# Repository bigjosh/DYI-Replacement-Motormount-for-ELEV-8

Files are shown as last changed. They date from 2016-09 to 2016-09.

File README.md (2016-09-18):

# DYI-Replacement-Motormount-for-ELEV-8
Files for making your own replacement motor mounts for the [Parallax ELEV-8 drone](https://www.parallax.com/product/elev-8)

###Crash!

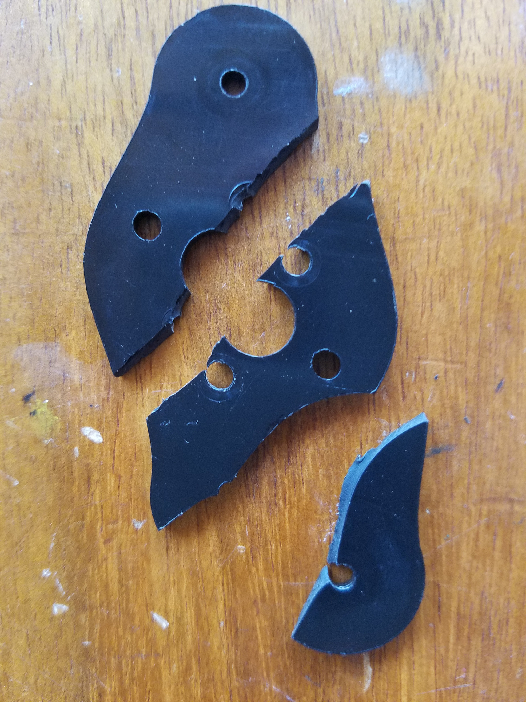
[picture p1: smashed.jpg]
smashed mount


I crashed my Parallax ELEV-8 drone (testing some stuff for Makerfaire NYC 2016!). 

The motormounts were smashed so I checked if I could...

###[Buy replacement motomounts directly from Parallax](https://www.parallax.com/product/721-80304)

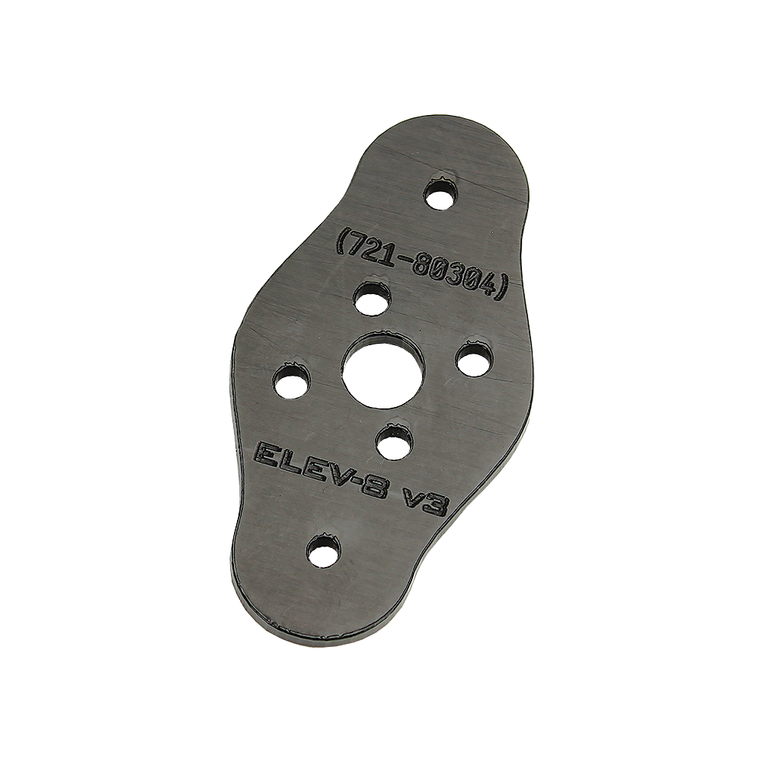
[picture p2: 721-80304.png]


Parallax sells the exact replacement part. They are made from 0.093 inches thick black acetal. They cost a reasonable for $3 each. 

Of course it is Friday night, so even if with an overnight shipping upgrade, I'd be grounded at least for the next 5 days. 

Maker Faire is 2 weeks away and there is (obviously) at least one crash-inducing problem to work out, so that wouldn't work. 

###Make replacement motor mounts!

I have a laser cutter, and converting bits into flat plastic shapes is exactly what laser cutters do best! Whoo hoo, I'll have my motormounts in no time!

###[Original SolidWorks file](721-80304.SLDPRT)

Parallax generously supplies files for all the parts in the ELEV-8!

But SolidWorks is [way too fancy](https://www.cati.com/blog/2015/04/how-much-does-solidworks-cost/) for me, so instead I import the part into...

###[OnShape](https://www.onshape.com/)

...which is a free and pretty nice web-based 3D cad program that happens to be able to import SolidWorks files. 

Here is what I ended up with...

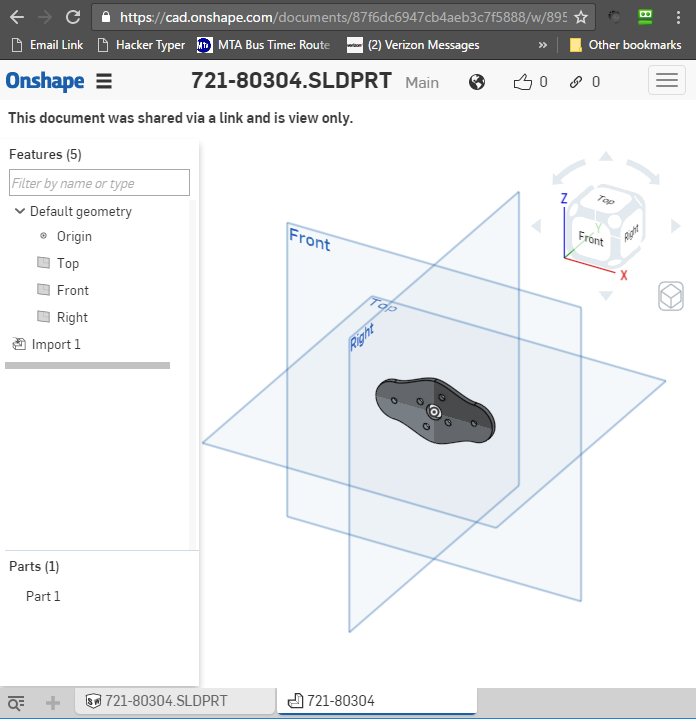
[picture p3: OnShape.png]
OnShape


https://cad.onshape.com/documents/87f6dc6947cb4aeb3c7f5888/w/89525256ab03b4d9a79cea25/e/45e0d6c32f898424b1c1b571

That looks familiar! I'll take 4 of those to go please!

I exported the face to a flat DXF R13 file...

[721-80304 - Face.dxf](721-80304 - Face.dxf)

Unfortunately my laser cutter does not speak DXF, but I can import the DXF into...

###[Inkscape](https://inkscape.org/en/)

...which is a free program that can import DXF and export the SVG files my laster cutter craves!

Sadly, Inkscape balked at the DXF (as often happens with DXF files) with a "POLYLINE encountered and ignored" error, so no joy on this path.

This must be my punishment for trying to use a cutting-edge web-based CAD tool. Serious people who want to get things done use
use serious CAD workstations running serious tools like...

###[Fusion 360 ](http://www.autodesk.com/products/fusion-360/overview)

...which is a free and nice desktop-based 3D cad program that can also import SolidWorks files.

Here is what I ended up with...

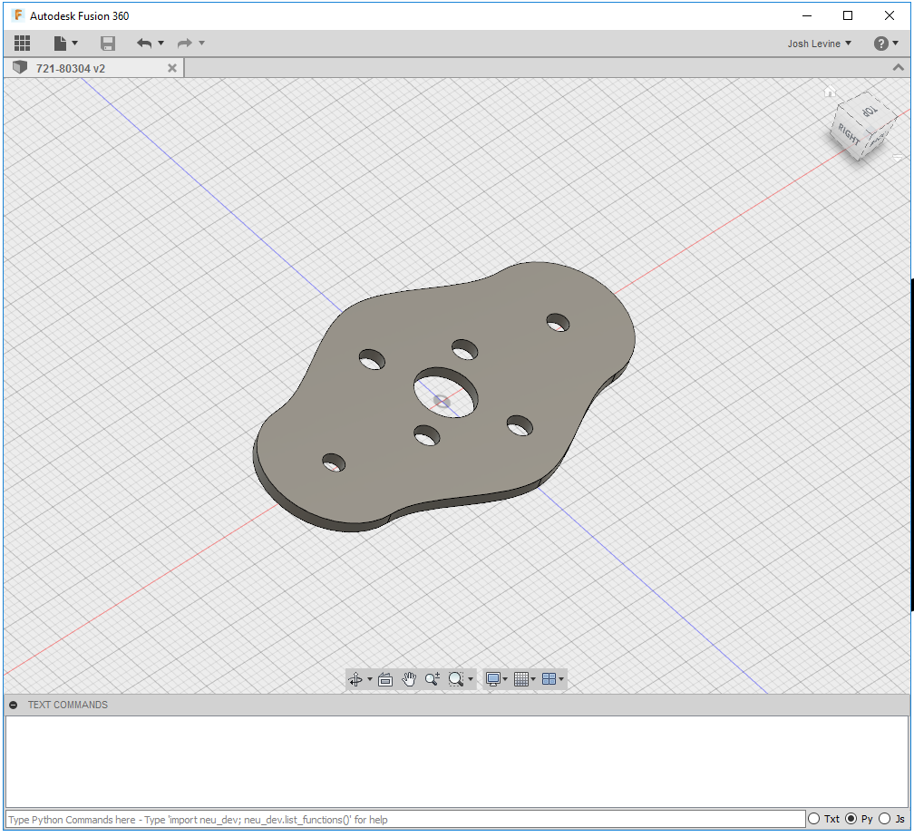
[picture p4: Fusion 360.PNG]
Fusion 360.PNG


http://a360.co/2clur11

There are my motomounts again!

I converted the face to a sketch (to 2D-ify it) and again exported the sketch as a DXF...

[721-80304 - Face F360.dxf](721-80304 - Face F360.dxf)

...which again seemed to make Inkscape vomit bits in the same way.

Hmmm... getting an SVG to send to the laser cutter is turning out to be a lot of hassle! We need some latteral thinking here!

While pondering my move, I notice out of the corner of my eye the very handy...

###[Othermill PCB cutter](https://othermachine.co/)

PCBs are sort of the right thickness and are probably strong enough, so if I can just make a PCB board that happens to 
be exactly the same shape as a motormount... Hmmm... A hack to be sure, but it should (could?) work!

Sadly the newest version of the Othermill software can not directly import a DXF file (maybe someday Othermill people? Please?).

Luckily, I know from experience that I can usually import DXF files into...

###[DipTrace PCB layout software](http://www.diptrace.com/)

...which happy complied! I specified to import the "visible" layer from the DXF into the "Board Outline" layer of the 
board and ended up with a motormount shaped board!....

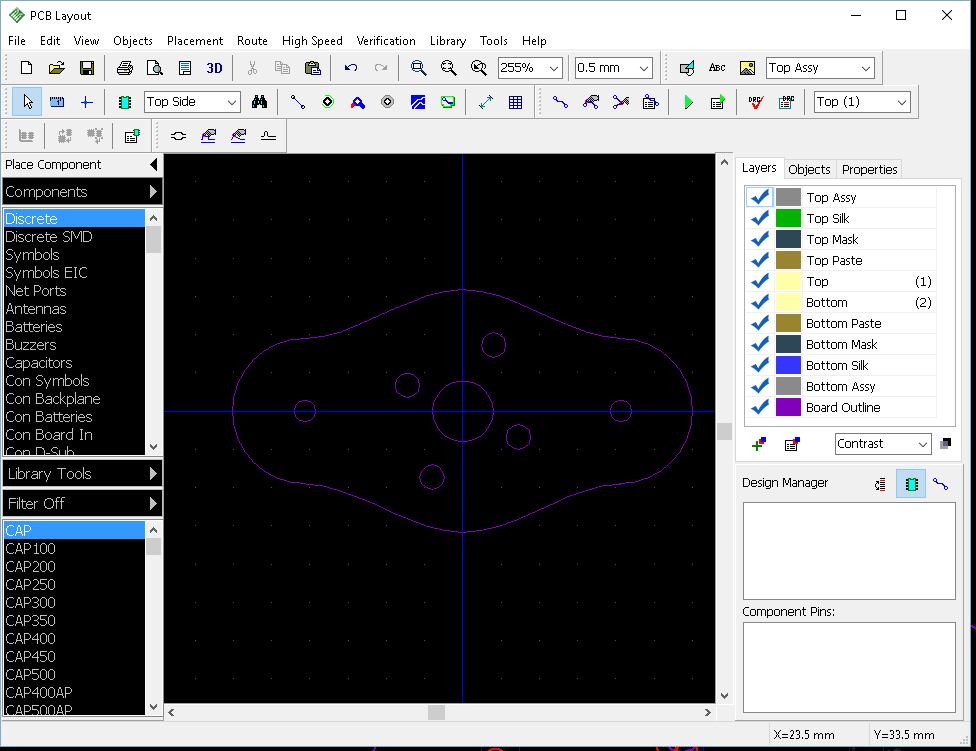
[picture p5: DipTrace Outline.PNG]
DipTrace Outline.PNG

[Motormount Board Outline with drill hit holes.dip](Motormount Board Outline with drill hit holes.dip)

Those are the boards I've been looking for! 

I quickly exported the board outline to a gerber file...

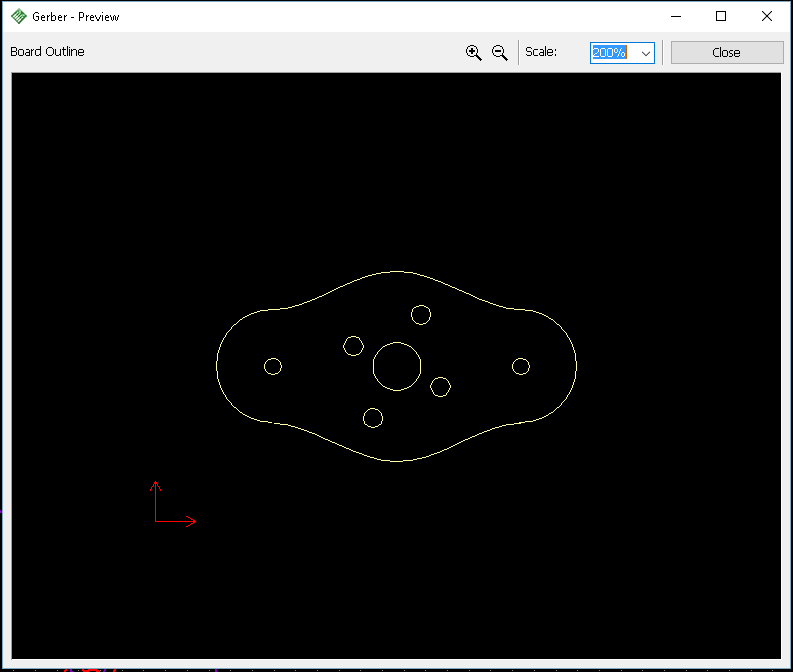
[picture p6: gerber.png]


[BoardOutline.gbr](BoardOutline.gbr)

...and jogged over to mill to load the file into...

###[Otherplan](https://othermachine.co/otherplan/)

...which is the software that reads in gerber files and actually cuts the boards on the Othermill.

Hey! I have a gerber and I want a board, so I the rest is just ceremony- right?

Turns out that Otherplan can not even load my gerber file! It [has not implemented the gerber "G85" command](https://othermachine.co/support/pcb/troubleshooting/) 
which is used to describe internal board cutouts. Boo Hoo (maybe someday OtherMill people? Please?).

Luckily those internal cutouts happen to be exactly round circles so if can convert the cutouts to...

###Drill hits

...I can create a gerber file for the outside outline of the shape, and then create an [Excelon drill hits file](https://en.wikipedia.org/wiki/Excellon_format) for the 
round interior cut-outs!

This turns out to be slightly tedious because there is no good way to replace a cutout with a matching hole. I have to manually measure the cutouts 
and then carefully manually place a drill hit in the center of each cutout, but eventually I end up with this... 

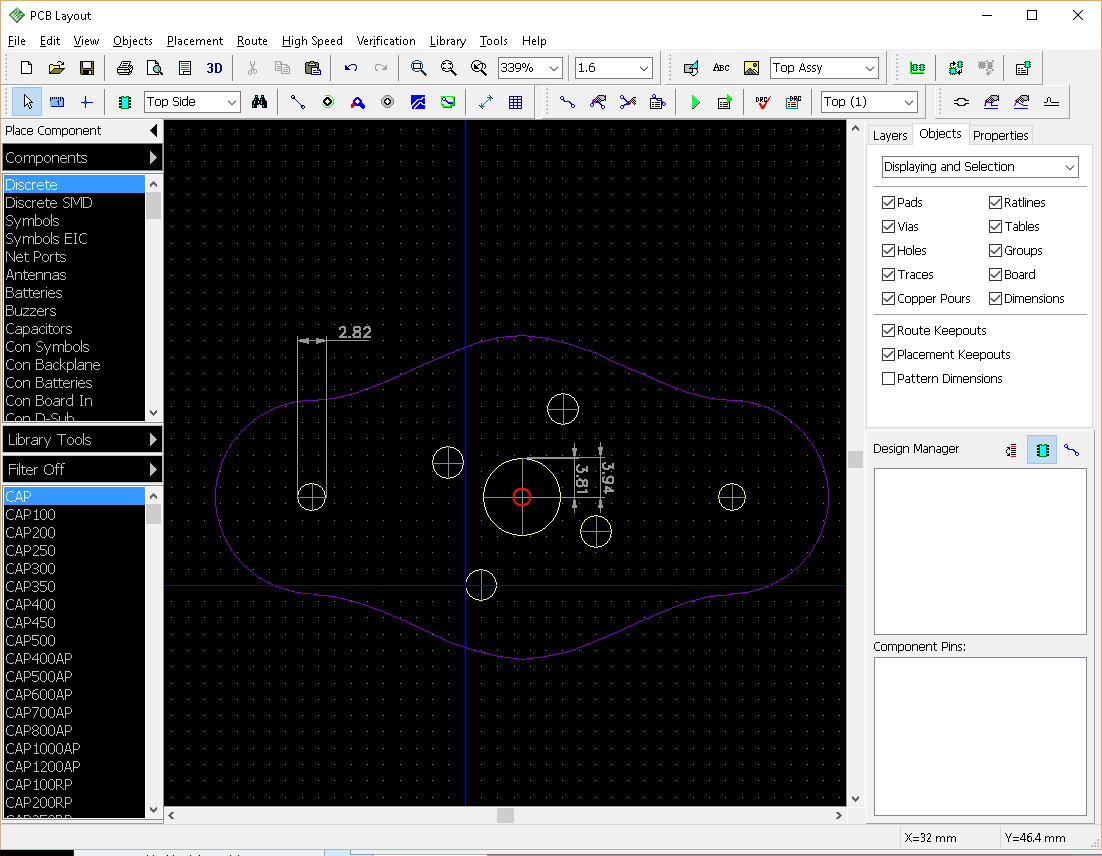
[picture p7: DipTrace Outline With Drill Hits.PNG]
DipTrace Outline With Drill Hits.PNG


...from which I can generate an outline gerber...

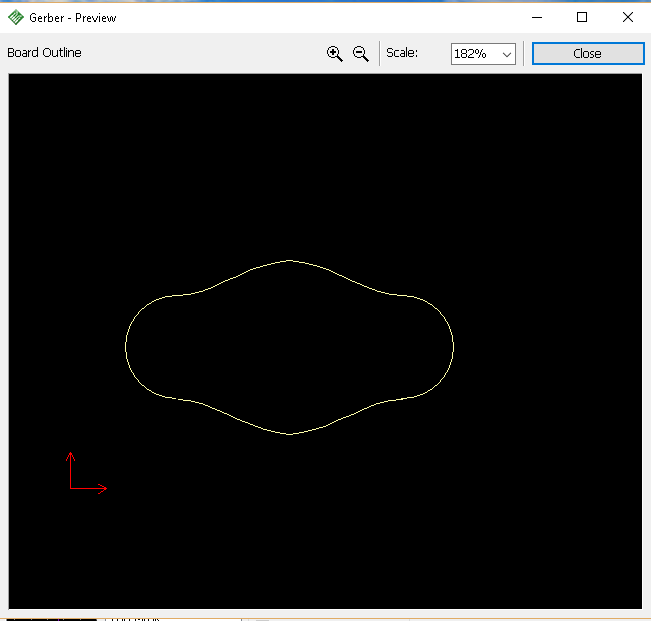
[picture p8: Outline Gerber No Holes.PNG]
Outline Gerber No Holes.PNG


[BoardOutline No Holes.gbr](BoardOutline No Holes.gbr)

...and a drill hits file...

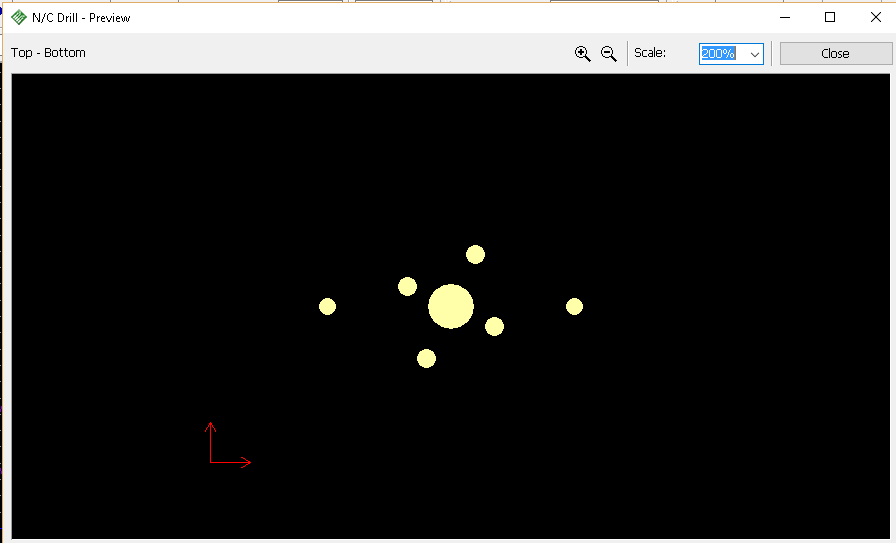
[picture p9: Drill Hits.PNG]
Drill Hits.PNG


[Through.drl](Through.drl)

###Ready to Cut!

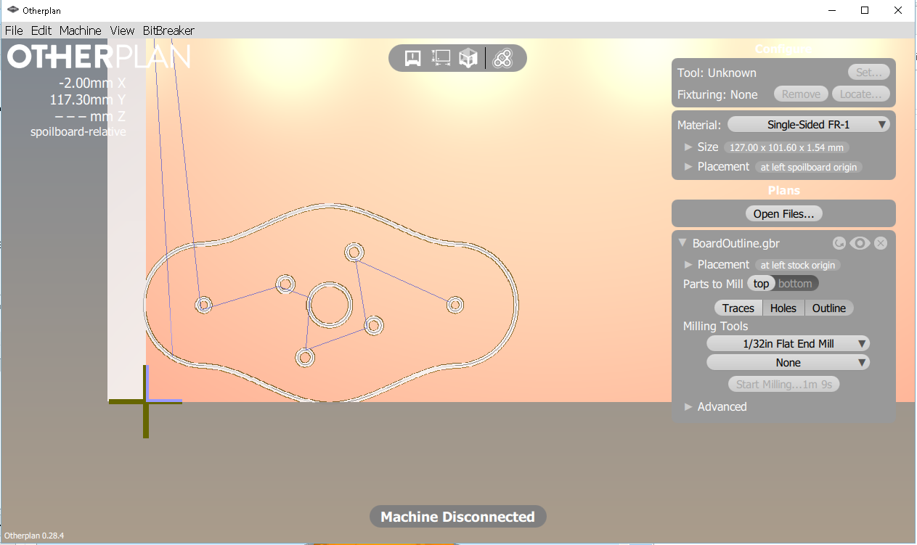
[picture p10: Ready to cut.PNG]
Ready to cut.PNG


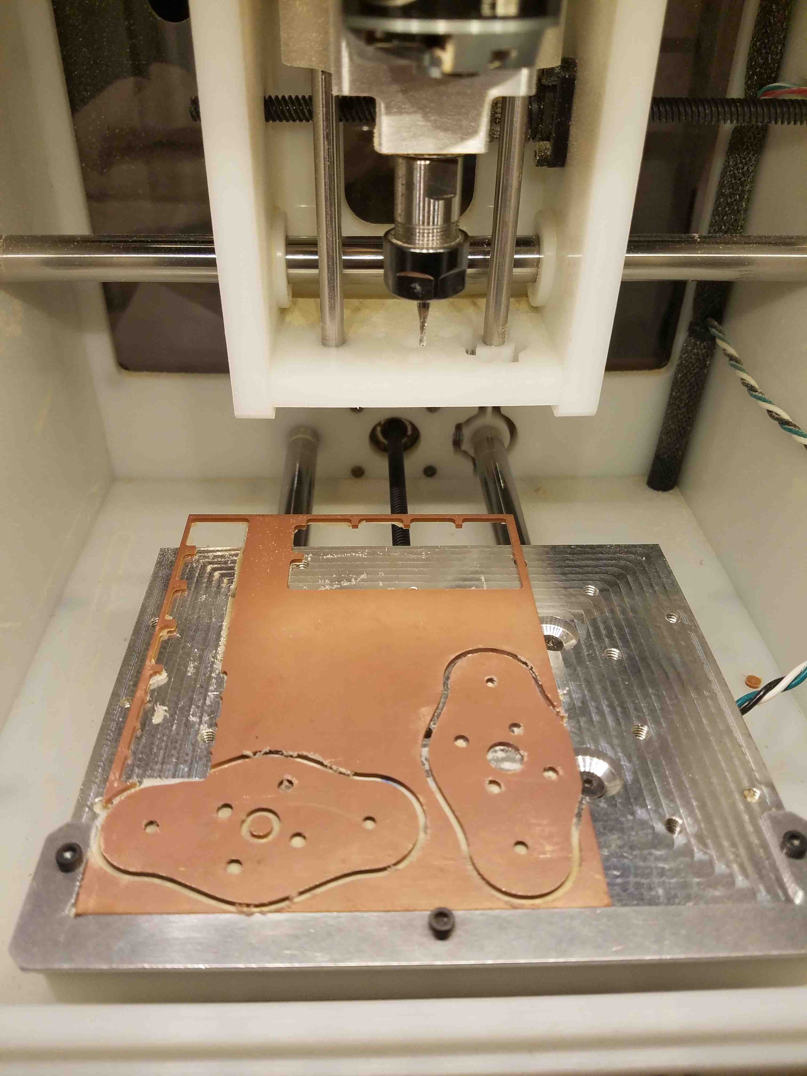
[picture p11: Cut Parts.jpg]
Cut Parts.jpg


###Oh happy day!

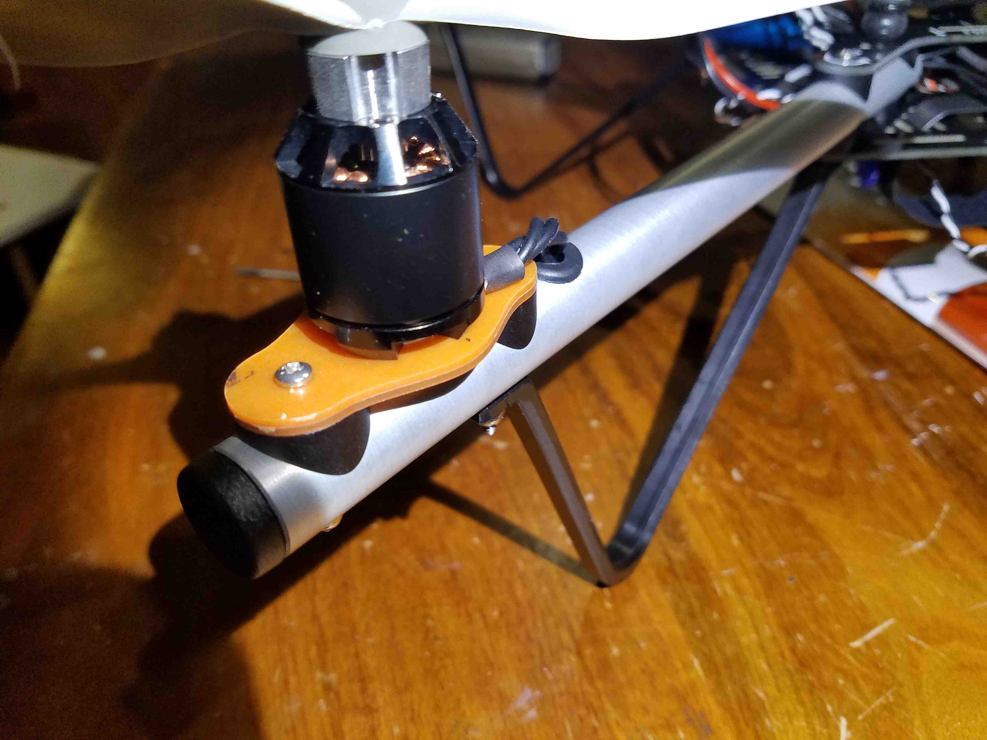
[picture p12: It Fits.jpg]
It Fits.jpg


(A few flights later, I can report that a stack of two 1.54mm FR1 PCBs work as a motor mount- at least for the placid maneuvers I am doing.)

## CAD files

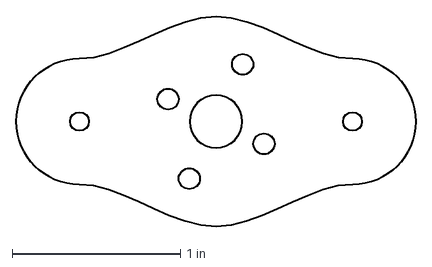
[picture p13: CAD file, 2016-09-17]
721-80304 - Face F360.dxf
2.38 x 1.25 in

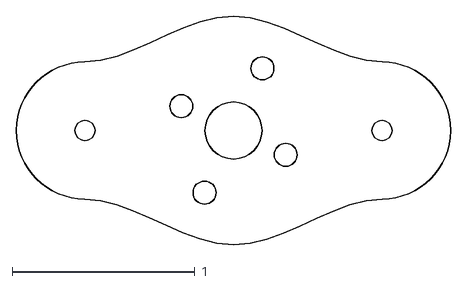
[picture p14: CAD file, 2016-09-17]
721-80304 - Face.dxf
2.38 x 1.25

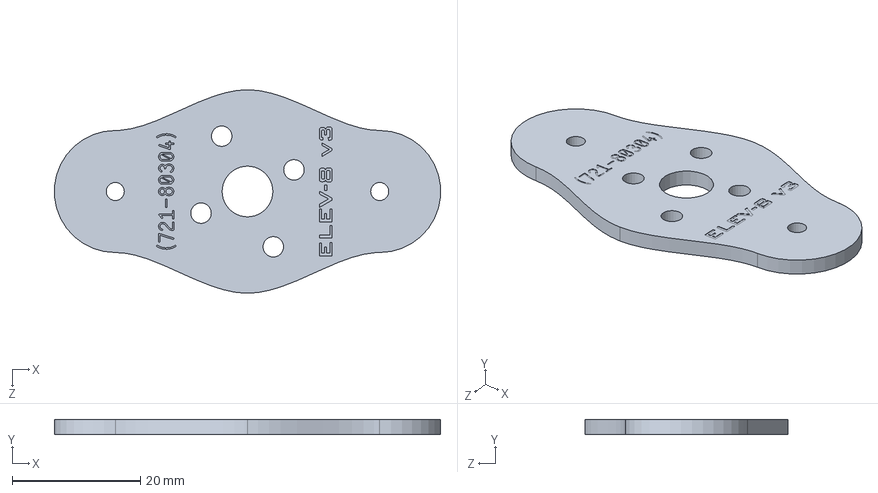
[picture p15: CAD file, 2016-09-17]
721-80304.SLDPRT
60.2 x 2.36 x 31.8 mm
